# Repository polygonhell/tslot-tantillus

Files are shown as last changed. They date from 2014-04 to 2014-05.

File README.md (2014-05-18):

tslot-tantillus
===============

THIS IS STILL A WIP,  Z Axis not tested and no place to mount a Z endstop right now.

Note horizontal TSlot must be 10 mm longer than the original derivative to retain original size, accounting for the offset of the 15mm openbeam rather than 20mm extrusion

i.e. original is 5+20 + 200 + 20+5 = 250mm, openbeam must be 5+15 + 210 + 15+5 = 250mm

Vertical beams extend the length of the case, and are therefore the same length

In my build, I dirlled the ends of the drive rods and couple the XY Motors directly too them. This is only practical if you have access to a lathe. You can choose to use standoffs and a coupler like the 2020 design but you will need to use Rod lengths ~5mm longer than the original 2020 TSlot design, rather than the ones specified here.

- OpenBeam lengths:
     - 9x (Horizontal 210mm) - cur one of them slightly undersized, it's used to mount the upper part of the Z axis
     - 4x (Vertical 335mm)

- All screws for frame assembly are M3x10mm, you'll need washers om the bolts going into the OpenBeam, I recommend cap head screws as they fit into the recesses provided for the XY Stepper mounts. If you are using the 40 mm standoffs from the original design then it doesn't matter.

- 8mm Shafting
     - 2x SFJ8-170 (8x170mm bearing shafts, same as Tantillus internal XY axis)
     - 2x SFJ8-230 (8x???mm Z axis), need to be short enough to not hit the X axis

- 5/16" Shafting - I started longer than required and curt them to size after test fitting
     - 2x --- TBD EXACT LENGTH 
     - 2x --- TBD EXACT LENGTH with holes drilled 56.5mm in from each end for a distance of 164mm hole to hole

- Hardware
     - Case assembly 
         - 120 M3x10mm screws - I used pan head, but it doesn't matter
         - 112 M3 Nuts
         - 112 M3 Washers

         - 4 M3x12 - For the ZAxis vertical bar retainers - probbaly best just to redesign for 10mm hardware
         - 4 M3 Nuts

     - X/Y Stepper Mounting 
         - 8 M3x10mm screws MUST be cap head or button head

     - X/Y axis - Same as the original
     - Extruder mount - Same as the original

     - Cable ZAxis - Same as the original - M4 hardware can be anywhere from about 12mm to 20mm
         - 3 M4x20
         - 1 M3x10

T-Slot frame for Tantillus 3D Printer

Initial Version Assumes:

- That you are using the cable version of the Z axis. If you aren't you will need to modify the lower Z adaptor for motor mount holes.
- 40mm standoffs for motor mounts, can purchase at mcmaster or print your own. Use 3x50mm bolts to attach motors.
- Misumi 2020 T-Slot lengths:
     - 8x HFS5-2020-200 (Horizontal 200mm)
     - 4x HFS5-2020-335 (Vertical 335mm)
     - HNKK5-5 (T-Slot nuts)
     - M5 10mm button head screw to affix panels to frame
- 8mm Shafting
     - 2x SFJ8-170 (8x170mm bearing shafts, same as Tantillus internal XY axis)
     - 2x SFJ8-230 (8x230mm bearing shafts, same as Tantillus Z axis)
- 5/16" Shafting
     - 2x 277mm
     - 2x 277mm with holes drilled 56.5mm in from each end for a distance of 164mm hole to hole
- Couplers
     - 2x Aluminum or simlar 5mm to 8mm shaft couplers
- Frame extra STL's:
     - spacers.STL - Motor 40mm standoffs if you want to use printed ones
     - knob_fixed.stl - Collar/manual nob for end of 5/16" rod (Use m3 set screw to hold in place on shaft.)
     - fanmount_fixed.stl x2 - Clips to attach fans to t-slot
     - lcdclamp_fixed.stl x2 - Clips to use as a rest for http://www.thingiverse.com/thing:28767
     - megaholder_fixed.stl - Plate for attaching arduino mega to t-slot
- The following files are provided for convenience:
     - ZlowerbracketfixedMETRIC_fixed.stl - Cable Z bracket modd'ed for M5 mounting (Use M5 16mm and M5 nuts)
     - ZupperbracketfixedMETRIC_fixed.stl - Cable Z bracket modd'ed for M5 mounting (Use M5 16mm and M5 nuts)

BEEFY Z Option:

- Is a more rigid Z axis mounting that has some other advantages such as being able to slide the upper and lower mount around and clamping bar end holders.
- BEEFY Z Printed parts
     - Zlowerbracket_BEEFY.stl - Cable Z bracket modd'ed for M5 mounting (Mounts directly into 2060 T-Slot)
     - Zupperbracket_BEEFY.stl - Cable Z bracket modd'ed for M5 mounting (Mounts directly into 2060 T-Slot)
- Misumi 2060 T-Slot Lengths:
     - 1x HFS5-2060-295 (Vertical 295mm [40mm short of main uprights)
- Misumi 90 degree brackets:
     - 4x HBLFSN5
I'm often in #reprap as goopyplastic if you have questions!

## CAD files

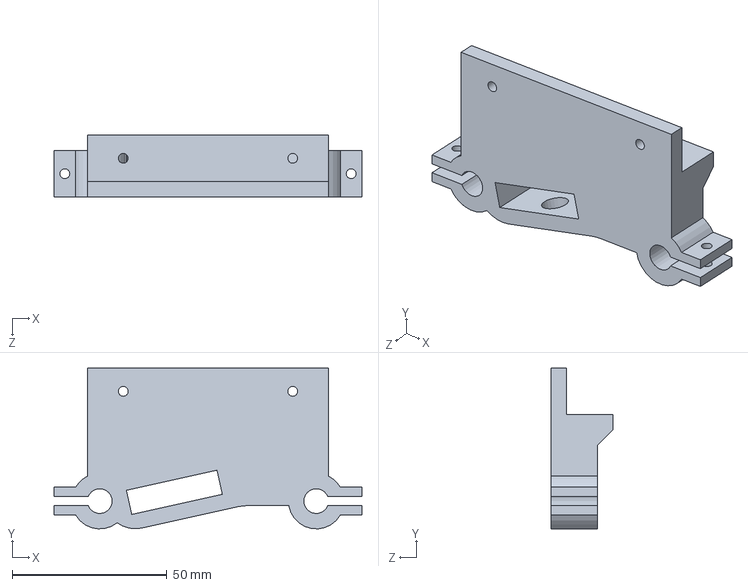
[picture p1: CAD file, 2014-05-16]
ZTop.SLDPRT
99.6 x 52.0 x 20.0 mm

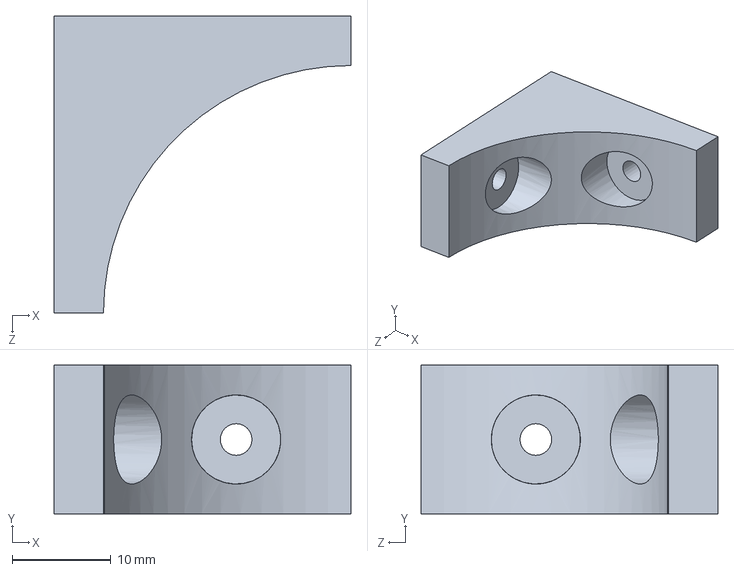
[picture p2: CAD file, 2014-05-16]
90degree.SLDPRT
30.0 x 15.0 x 30.0 mm

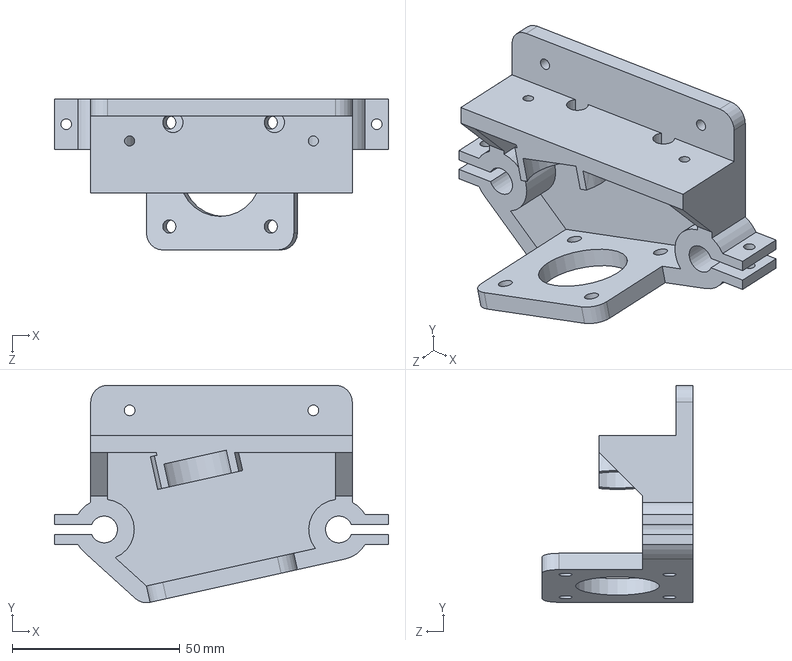
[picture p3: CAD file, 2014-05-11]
Zbottom.SLDPRT
99.6 x 64.8 x 45.0 mm

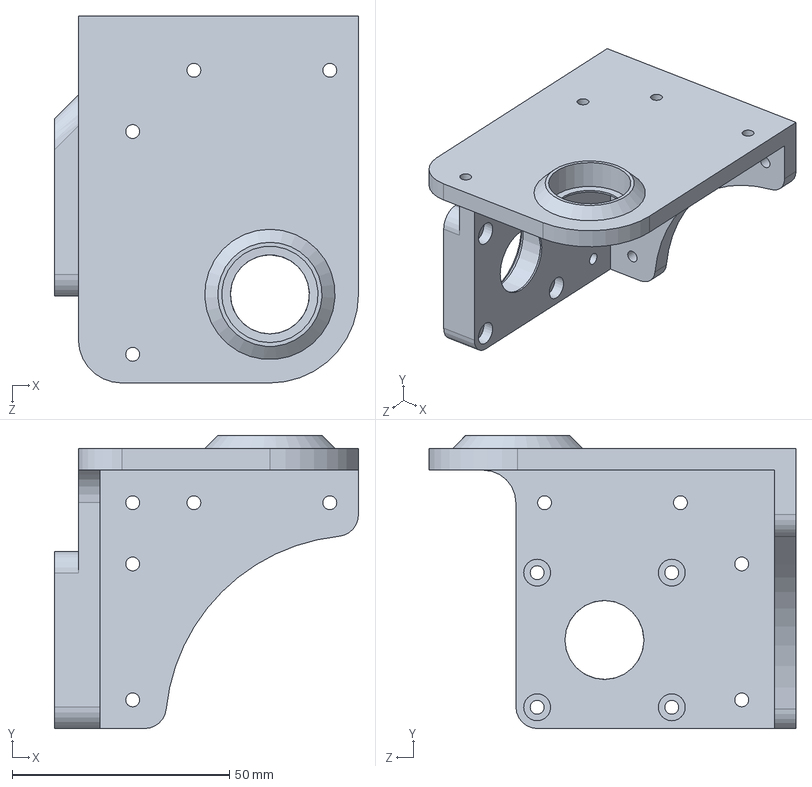
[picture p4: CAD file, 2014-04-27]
Rear_Right.SLDPRT
70.0 x 67.5 x 84.5 mm

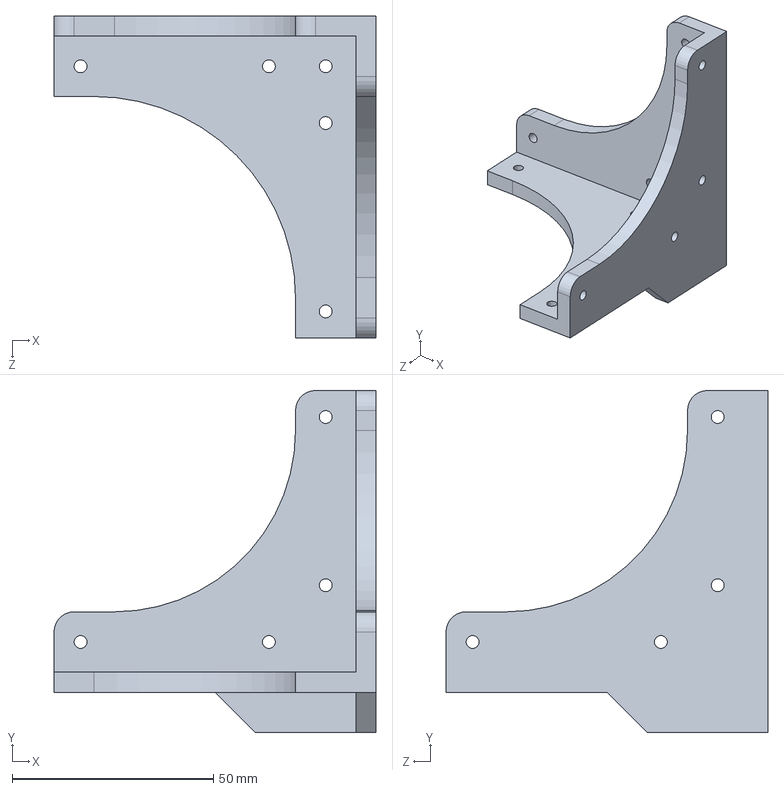
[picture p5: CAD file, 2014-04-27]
Bottom.SLDPRT
80.0 x 85.0 x 80.0 mm

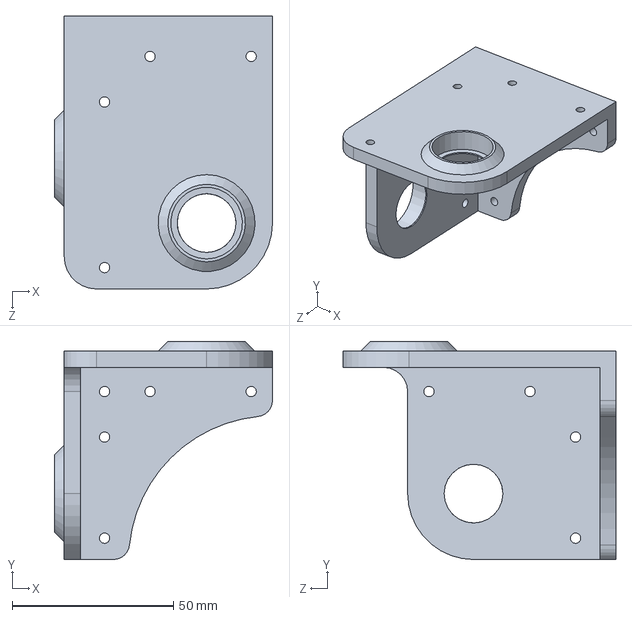
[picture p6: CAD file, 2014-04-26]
Front_Left.SLDPRT
67.5 x 67.5 x 84.5 mm

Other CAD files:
Rear_Left.SLDPRT
Front_Right.SLDPRT
90degree.STL
Bottom.STL
Front_Left.STL
Front_Right.STL
Rear_Left.STL
Rear_Right.STL
ZTop.STL
Zbottom.STL

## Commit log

2014-04-26 First 3 pieces
    [Front_Left.SLDPRT, Front_Left.STL, Front_Right.SLDPRT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]
2014-04-27 Add remaining rear and Bottom pieces
    minor changes to stepper mount on rear pieces
    [Bottom.SLDPRT, Bottom.STL, Rear_Left.SLDPRT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]
2014-04-29 remove 2020 files and update readme
    [panel_combine_BOTTOM.STL, panel_combine_FRONT_LEFT.STL, panel_combine_FRONT_RIGHT.STL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]
2014-05-11 Add ZBottom
    [Zbottom.SLDPRT, Zbottom.STL]
2014-05-13 Add Ztop
    Initial test piece, need to check alignment, and add limit switch
    [ZTop.SLDPRT, ZTop.STL]
2014-05-16 Correct bearing position for ZTop
    Add 90 degree piece for Z cross beam
    [90degree.SLDPRT, 90degree.STL, ZTop.SLDPRT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]
